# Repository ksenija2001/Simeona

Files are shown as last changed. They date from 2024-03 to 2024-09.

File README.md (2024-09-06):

## Components

| Name | Datasheet | Function  | Quantity |
|:-:|:-:|:-:|:-:|
|  DCGM-3865-12V-EN-240RPM | [datasheet](https://www.waveshare.com/wiki/DCGM-3865-12V-EN-240RPM) | Motor | 2 |
|  NUCLEO-F411RE |  [datasheet](https://www.st.com/content/ccc/resource/technical/document/data_brief/c8/3c/30/f7/d6/08/4a/26/DM00105918.pdf/files/DM00105918.pdf/jcr:content/translations/en.DM00105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)|  Microcontroller | 1 | 
|  Raspberry Pi 4B, 4GB |  [datasheet](https://datasheets.raspberrypi.com/rpi4/raspberry-pi-4-datasheet.pdf) |  Mini-PC |  1 |
|  ROB-14451 |  [datasheet](https://eu.mouser.com/datasheet/2/830/TB6612FNG_datasheet_en_20141001-2528981.pdf) |  Driver | 1 |
|  Slamtec RPLIDAR A2 |  [datasheet](https://bucket-download.slamtec.com/f65f8e37026796c56ddd512d33c7d4308d9edf94/LD310_SLAMTEC_rplidar_datasheet_A2M12_v1.0_en.pdf) |  LIDAR | 1 |
|  TOF |  [datasheet](https://www.waveshare.com/wiki/TOF_Laser_Range_Sensor) |  TOF | 1 |
|  Raspberry Pi Camera Module 3 | |  Camera | 1 |
|  DC/DC XL4015 |  Output 1.25-36V, 5A  |  Step down | 1 |
|  3s Battery  | 2200mah, 11.1V |  Battery | 1 |
|  USB A - USB mini B |  |  Cable | 1 |

## Additional material

<center>
  
| Function | Specification | Quantity  |  Placement |
|:-:|:-:|:-:| :-:|
|  O-ring | 64x3mm | 6 | On wheels |
|  Nucleo mounting screws |  M3x8mm |  3 | Middle level | 
|  RPi4 mounting screws |  M2x20mm |  4 |  Middle level |
|  Step down mounting screws |  M3x10mm |  2 | Bottom level |
|  LIDAR mounting screws |  M3x10mm |  4 | Top level |
|  Motor mounting screws |  M3x16mm |  8 | Bottom level |
|  TOF mounting screws |  M2x10mm |  2 | Bottom level |
|  Battery cover screws |  M3x12mm |  2 | Battery cover |
|  Connecting screws |  M3x16mm |  12 | Between levels |
|  Connecting nuts |  M3 |  12 | Between levels |
|  Insert nut |  M3 |  7 | For RPi4 and Nucleo |

</center>

## CAD

All parts which make up the construction are in the folder [parts](parts).

The following table contains all information about 3D printing the provided parts.
A 0.4mm nozzle was used, everything was printed from PLA on a Bambu A1 Mini.

| Name | Infill | Walls  |  Layer height | Plastic |
|:-:|:-:|:-:| :-:| :-:|
|  Bottom | 20 | 2 | 0.2 | 123g |
|  Middle | 20 | 2 | 0.2 |  63g |
|  Top | 20 | 2 | 0.2 |  60g |
|  Wheel  | 40 | 2 | 0.2 |  20g |
|  Battery cover | 15 | 2 | 0.2 | 17g |

TIP: Hot glue the nut holes when you insert them so they don't fall out every time you have to disassemble it.

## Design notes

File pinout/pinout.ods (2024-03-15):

 | Name | Type | Signal | Label | AF0 | AF1 | AF2 | AF3 | AF4 | AF5 | AF6 | AF7 | AF8 | AF9 | AF10 | AF11 | AF12
1 | VBAT | Power
2 | PC13-ANTI_TAMP | I/O | GPIO_EXTI13 | B1 [Blue PushButton]
3 | PC14-OSC32_IN | I/O | RCC_OSC32_IN
4 | PC15-OSC32_OUT | I/O | RCC_OSC32_OUT
5 | PH0 - OSC_IN | I/O | RCC_OSC_IN
6 | PH1 - OSC_OUT | I/O | RCC_OSC_OUT
7 | NRST | Reset
8 | PC0 | I/O
9 | PC1 | I/O
10 | PC2 | I/O |  |  |  |  |  |  |  | SPI2_MISO | I2S2_ext_SD
11 | PC3 | I/O |  |  |  |  |  |  |  | I2S2_SD/SPI2_MOSI
12 | VSSA | Power
13 | VDDA | Power
14 | PA0-WKUP | I/O |  |  |  | TIM2_CH1/TIM2_ETR | TIM5_CH1 |  |  |  |  | USART2_CTS
15 | PA1 | I/O |  |  |  | TIM2_CH2 | TIM5_CH2 |  |  | I2S4_SD/SPI4_MOSI |  | USART2_RTS
16 | PA2 | I/O |  |  |  | TIM2_CH3 | TIM5_CH3 | TIM9_CH1 |  | I2S_CKIN |  | USART2_TX
17 | PA3 | I/O |  |  |  | TIM2_CH4 | TIM5_CH4 | TIM9_CH2 |  | I2S2_MCK |  | USART2_RX
18 | VSS | Power
19 | VDD | Power
20 | PA4 | I/O |  |  |  |  |  |  |  | I2S1_WS/SPI1_NSS | I2S3_WS/SPI3_NSS | USART2_CK
21 | PA5 | Output | GPIO_Output | LD2 [Green Led] |  | TIM2_CH1/TIM2_ETR |  |  |  | I2S1_CK/SPI1_SCK
22 | PA6 | I/O |  |  |  | TIM1_BKIN | TIM3_CH1 |  |  | SPI1_MISO | I2S2_MCK |  |  |  |  |  | SDIO_CMD
23 | PA7 | I/O |  |  |  | TIM1_CH1N | TIM3_CH2 |  |  | I2S1_SD/SPI1_MOSI
24 | PC4 | I/O
25 | PC5 | I/O
26 | PB0 | I/O |  |  |  | TIM1_CH2N | TIM3_CH3 |  |  |  | I2S5_CK/SPI5_SCK
27 | PB1 | I/O |  |  |  | TIM1_CH3N | TIM3_CH4 |  |  |  | I2S5_WS/SPI5_NSS
28 | PB2 | I/O
29 | PB10 | I/O |  |  |  | TIM2_CH3 |  |  | I2C2_SCL | I2S2_CK/SPI2_SCK | I2S3_MCK |  |  |  |  |  | SDIO_D7
30 | VCAP1 | Power
31 | VSS | Power
32 | VDD | Power
33 | PB12 | I/O |  |  |  | TIM1_BKIN |  |  | I2C2_SMBA | I2S2_WS/SPI2_NSS | I2S4_WS/SPI4_NSS | I2S3_CK/SPI3_SCK
34 | PB13 | I/O |  |  |  | TIM1_CH1N |  |  |  | I2S2_CK/SPI2_SCK | I2S4_CK/SPI4_SCK
35 | PB14 | I/O |  |  |  | TIM1_CH2N |  |  |  | SPI2_MISO | I2S2_ext_SD |  |  |  |  |  | SDIO_D6
36 | PB15 | I/O |  |  | RTC_REFIN | TIM1_CH3N |  |  |  | I2S2_SD/SPI2_MOSI |  |  |  |  |  |  | SDIO_CK
37 | PC6 | I/O |  |  |  |  | TIM3_CH1 |  |  | I2S2_MCK |  |  | USART6_TX |  |  |  | SDIO_D6
38 | PC7 | I/O |  |  |  |  | TIM3_CH2 |  |  | I2S2_CK/SPI2_SCK | I2S3_MCK |  | USART6_RX |  |  |  | SDIO_D7
39 | PC8 | I/O |  |  |  |  | TIM3_CH3 |  |  |  |  |  | USART6_CK |  |  |  | SDIO_D0
40 | PC9 | I/O |  |  | RCC_MCO_2 |  | TIM3_CH4 |  | I2C3_SDA | I2S_CKIN |  |  |  |  |  |  | SDIO_D1
41 | PA8 | I/O |  |  | RCC_MCO_1 | TIM1_CH1 |  |  | I2C3_SCL |  |  | USART1_CK |  |  | USB_OTG_FS_SOF |  | SDIO_D1
42 | PA9 | I/O |  |  |  | TIM1_CH2 |  |  | I2C3_SMBA |  |  | USART1_TX |  |  | USB_OTG_FS_VBUS |  | SDIO_D2
43 | PA10 | I/O |  |  |  | TIM1_CH3 |  |  |  |  | I2S5_SD/SPI5_MOSI | USART1_RX |  |  | USB_OTG_FS_ID
44 | PA11 | I/O |  |  |  | TIM1_CH4 |  |  |  |  | SPI4_MISO | USART1_CTS | USART6_TX |  | USB_OTG_FS_DM
45 | PA12 | I/O |  |  |  | TIM1_ETR |  |  |  |  | SPI5_MISO | USART1_RTS | USART6_RX |  | USB_OTG_FS_DP
46 | PA13 | I/O | SYS_JTMS-SWDIO | TMS | SYS_JTMS-SWDIO
47 | VSS | Power
48 | VDD | Power
49 | PA14 | I/O | SYS_JTCK-SWCLK | TCK | SYS_JTCK-SWCLK
50 | PA15 | I/O |  |  | SYS_JTDI | TIM2_CH1/TIM2_ETR |  |  |  | I2S1_WS/SPI1_NSS | I2S3_WS/SPI3_NSS | USART1_TX
51 | PC10 | I/O |  |  |  |  |  |  |  |  | I2S3_CK/SPI3_SCK |  |  |  |  |  | SDIO_D2
52 | PC11 | I/O |  |  |  |  |  |  |  | I2S3_ext_SD | SPI3_MISO |  |  |  |  |  | SDIO_D3
53 | PC12 | I/O |  |  |  |  |  |  |  |  | I2S3_SD/SPI3_MOSI |  |  |  |  |  | SDIO_CK
54 | PD2 | I/O |  |  |  |  | TIM3_ETR |  |  |  |  |  |  |  |  |  | SDIO_CMD
55 | PB3 | I/O | SYS_JTDO-SWO | SWO | SYS_JTDO-SWO | TIM2_CH2 |  |  |  | I2S1_CK/SPI1_SCK | I2S3_CK/SPI3_SCK | USART1_RX |  | I2C2_SDA
56 | PB4 | I/O |  |  | SYS_JTRST |  | TIM3_CH1 |  |  | SPI1_MISO | SPI3_MISO | I2S3_ext_SD |  | I2C3_SDA |  |  | SDIO_D0
57 | PB5 | I/O |  |  |  |  | TIM3_CH2 |  | I2C1_SMBA | I2S1_SD/SPI1_MOSI | I2S3_SD/SPI3_MOSI |  |  |  |  |  | SDIO_D3
58 | PB6 | I/O |  |  |  |  | TIM4_CH1 |  | I2C1_SCL |  |  | USART1_TX
59 | PB7 | I/O |  |  |  |  | TIM4_CH2 |  | I2C1_SDA |  |  | USART1_RX |  |  |  |  | SDIO_D0
60 | BOOT0 | Boot
61 | PB8 | I/O |  |  |  |  | TIM4_CH3 | TIM10_CH1 | I2C1_SCL |  | I2S5_SD/SPI5_MOSI |  |  | I2C3_SDA |  |  | SDIO_D4
62 | PB9 | I/O |  |  |  |  | TIM4_CH4 | TIM11_CH1 | I2C1_SDA | I2S2_WS/SPI2_NSS |  |  |  | I2C2_SDA |  |  | SDIO_D5
63 | VSS | Power
64 | VDD | Power

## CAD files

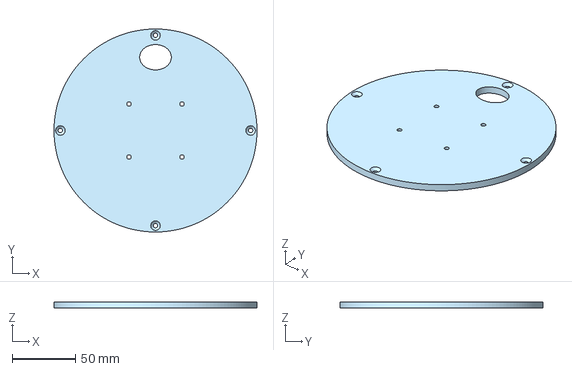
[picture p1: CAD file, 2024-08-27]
parts/Top.3mf
160.0 x 160.0 x 5.00 mm

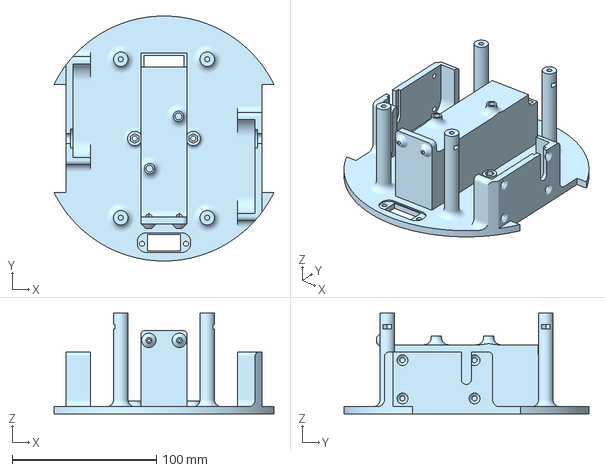
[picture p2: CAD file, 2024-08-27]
parts/Bottom.3mf
152.6 x 170.0 x 70.0 mm

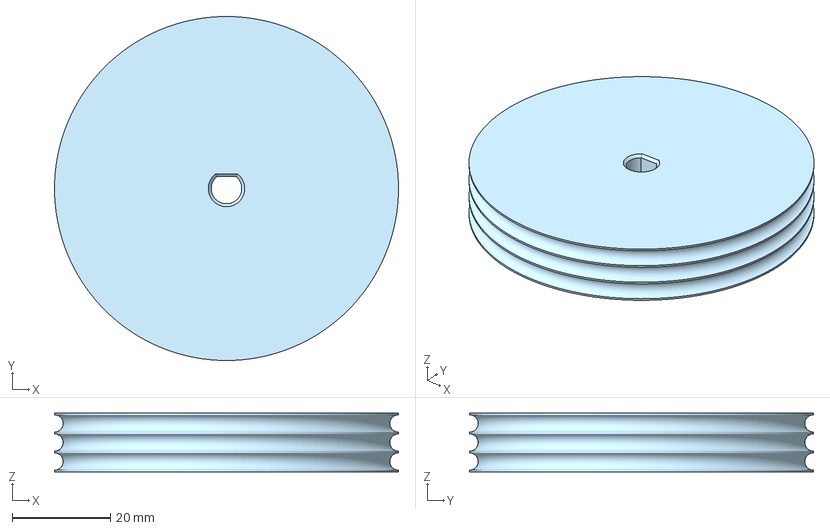
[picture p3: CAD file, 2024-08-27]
parts/Wheel.3mf
70.0 x 70.0 x 12.0 mm

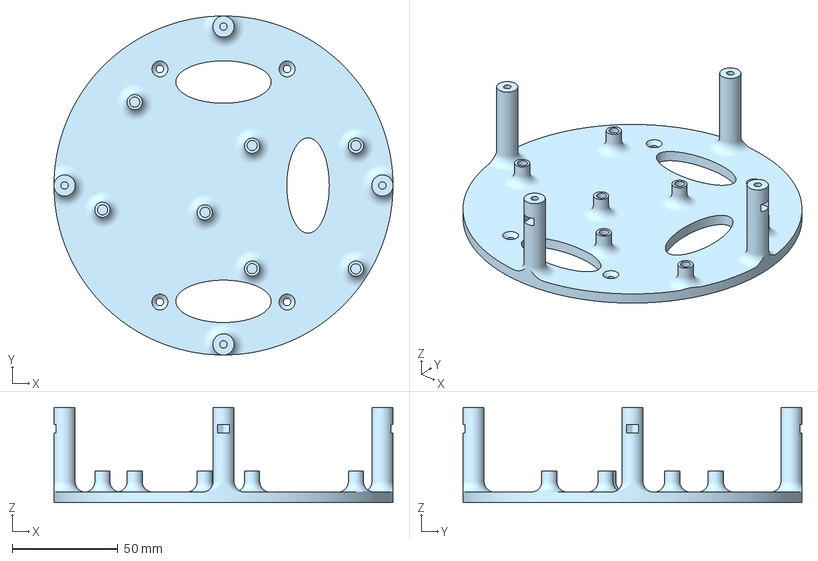
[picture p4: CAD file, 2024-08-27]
parts/Middle.3mf
160.0 x 160.0 x 45.0 mm

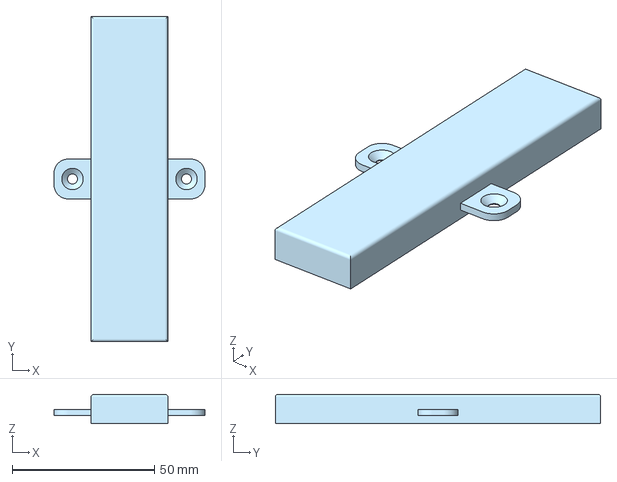
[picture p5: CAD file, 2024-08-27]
parts/Battery_Cover.3mf
53.0 x 114.2 x 10.3 mm

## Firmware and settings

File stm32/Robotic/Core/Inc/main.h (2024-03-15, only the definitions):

#define B1_Pin GPIO_PIN_13
#define B1_GPIO_Port GPIOC
#define TMS_Pin GPIO_PIN_13
#define TMS_GPIO_Port GPIOA
#define TCK_Pin GPIO_PIN_14
#define TCK_GPIO_Port GPIOA
#define SWO_Pin GPIO_PIN_3
#define SWO_GPIO_Port GPIOB

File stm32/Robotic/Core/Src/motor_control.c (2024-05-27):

/*
 * motor_control.c
 *
 *  Created on: Mar 14, 2024
 *      Author: xenia
 */

#include "motor_control.h"

float q0;
float q1;
float q2;

volatile uint32_t interrupt_counter = 0;
float send_odom[7];


sOutput_t BI2  = { .port = GPIOB, .pin = 10 };
sOutput_t BI1  = { .port = GPIOC, .pin = 7 };
sOutput_t AI2  = { .port = GPIOA, .pin = 5};
sOutput_t AI1  = { .port = GPIOB, .pin = 6};
sOutput_t PWMA = { .port = GPIOA, .pin = 0};
sOutput_t PWMB = { .port = GPIOA, .pin = 1};

sMotor_t left_motor = {
		.target_speed = 0,
		.current_speed = 0,
		.control_PWM = 0,
		.errors = {0, 0, 0},
		.Kp = 8,
		.Ki = 0.08,
		.Kd = 0.12,
};
sMotor_t right_motor= {
		.target_speed = 0,
		.current_speed = 0,
		.control_PWM = 0,
		.errors = {0, 0, 0},
		.Kp = 8,
		.Ki = 0.08,
		.Kd = 0.12,
};



// TIM2 CH1 and CH2 configuration as PWM output
// Driver direction pins configuration
void Motors_Init()
{
	left_motor.Compute_PID = Compute_PID;
	right_motor.Compute_PID = Compute_PID;

	// Enabe GPIOA (PWM port), GPIOB and GPIOC clock source
	RCC->AHB1ENR |= ( RCC_AHB1ENR_GPIOAEN );
	RCC->AHB1ENR |= ( RCC_AHB1ENR_GPIOBEN );
	RCC->AHB1ENR |= ( RCC_AHB1ENR_GPIOCEN );

	// Enable TIM2 (PWM source) clock source - 84Mhz
	RCC->APB1ENR |= ( RCC_APB1ENR_TIM2EN );

	// Set PWM source channel pins PA0 (CH1) and PA1 (CH2)
	// to alternate function mode AF1
	PWMA.port->MODER &= ~(0b11 << 2*PWMA.pin);
	PWMA.port->MODER |=  (0b10 << 2*PWMA.pin);
	PWMB.port->MODER &= ~(0b11 << 2*PWMB.pin);
	PWMB.port->MODER |=  (0b10 << 2*PWMB.pin);

	PWMA.port->AFR[0] &= ~(0b1111 << 4*PWMA.pin);
	PWMA.port->AFR[0] |=  (0b0001 << 4*PWMA.pin);
	PWMB.port->AFR[0] &= ~(0b1111 << 4*PWMB.pin);
	PWMB.port->AFR[0] |=  (0b0001 << 4*PWMB.pin);

	// Autoreload value determines the frequency of
	// the PWM signal - 84MHz -> 20kHz
	TIM2->PSC = 1 - 1;
	TIM2->ARR = PWM_ARR;

	// PWM mode 1 - channel is active as long as
	// TIM2->CNT < TIM2->CCR1 - during the timer period
	TIM2->CCMR1 &= ~(0b111 << TIM_CCMR1_OC1M_Pos | 0b111 << TIM_CCMR1_OC2M_Pos);
	TIM2->CCMR1 |=  (0b110 << TIM_CCMR1_OC1M_Pos | 0b110 << TIM_CCMR1_OC2M_Pos);

	// Enable preload for TIM2
	TIM2->CCMR1 |= (0b1 << TIM_CCMR1_OC1PE_Pos | 0b1 << TIM_CCMR1_OC2PE_Pos);

	// Enable autoreload for TIM2
	TIM2->CR1 |= (0b1 << TIM_CR1_ARPE_Pos);

	// Enable automatic update of registers
	TIM2->EGR |= (0b1 << TIM_EGR_UG_Pos);

	// Enable capture/compare as output
	// (PWM output to driver) for CH1 and CH2
	// Default falling edge mode
	TIM2->CCER |= (0b1 << TIM_CCER_CC1E_Pos | 0b1 << TIM_CCER_CC2E_Pos);

	// Enable PWM generation in default edge aligned mode
	TIM2->CR1 |= (0b1 << TIM_CR1_CEN_Pos);



	// Configure pins for driver direction as
	// general purpose output pins
	BI2.port->MODER &= ~(0b11 << 2*BI2.pin);
	BI2.port->MODER |=  (0b01 << 2*BI2.pin);

	BI1.port->MODER &= ~(0b11 << 2*BI1.pin);
	BI1.port->MODER |=  (0b01 << 2*BI1.pin);

	AI1.port->MODER &= ~(0b11 << 2*AI1.pin);
	AI1.port->MODER |=  (0b01 << 2*AI1.pin);

	AI2.port->MODER &= ~(0b11 << 2*AI2.pin);
	AI2.port->MODER |=  (0b01 << 2*AI2.pin);

	// Configure pins for driver direction as
	// output push pull (reset state)
	BI2.port->OTYPER &=  ~(0b1 << BI2.pin);
	BI1.port->OTYPER &=  ~(0b1 << BI1.pin);
	AI1.port->OTYPER &=  ~(0b1 << AI1.pin);
	AI2.port->OTYPER &=  ~(0b1 << AI2.pin);
}

// Configures timer TIM11 with interrupt every 10ms which executes
// PID computation and updates odometry data
void PID_Odom_Interrupt_Init()
{
	// Lower priority than UART IRQHandler and UART buffer checking
	uint32_t tim10_pri_encoding = NVIC_EncodePriority(0, 1, 2);

	// Clock source for TIM10
	RCC->APB2ENR |= ( RCC_APB2ENR_TIM10EN );

	// Clock setup for TIM10, 10ms
	TIM10->PSC = 13 - 1;
	TIM10->ARR = 60000 - 1;

	// Enable immediate update of register on counter
	TIM10->EGR |= ( TIM_EGR_UG );

	// Enable interrupts for TIM10
	TIM10->DIER |= ( TIM_DIER_UIE );

	// Enable counter for TIM10
	TIM10->CR1 |= ( TIM_CR1_CEN );

	// Setup the NVIC to enable interrupts.
	NVIC_SetPriorityGrouping( 0 );
	NVIC_SetPriority( TIM1_UP_TIM10_IRQn, tim10_pri_encoding );
	NVIC_EnableIRQ( TIM1_UP_TIM10_IRQn );
}

void TIM1_UP_TIM10_IRQHandler(void)
{;
	interrupt_counter += 10;

	// Calculates new position and orientation based on encoder output
	// and sends odometry data via UART
	if( interrupt_counter % ODOM_TIME == 0 ){
		sOdom_t* odom = Read_Encoders();

		send_odom[0] = odom->x;
		send_odom[1] = odom->y;
		send_odom[2] = odom->theta;
		send_odom[3] = odom->left_speed;
		send_odom[4] = odom->right_speed;
		send_odom[5] = odom->left_inc;
		send_odom[6] = odom->right_inc;

		left_motor.current_speed = odom->left_speed;
		right_motor.current_speed = odom->right_speed;

		Send_Command(ODOM_TRANSMIT, send_odom, sizeof(send_odom));
	}

	// Calculates speed loop PID and sends the output to the driver
	if( interrupt_counter % PID_TIME == 0 ){
		left_motor.Compute_PID(&left_motor);
		right_motor.Compute_PID(&right_motor);

		Set_Motor_Direction(left_motor.control_PWM, right_motor.control_PWM);
		Set_Motor_PWM(abs(left_motor.control_PWM), abs(right_motor.control_PWM));
	}

	// Clears interrupt flag so that other interrupts can work
	TIM10->SR &= ~TIM_SR_UIF;
}

// Sets target speed for speed loop
void Set_Motor_Speed(float left, float right)
{
	left_motor.target_speed = left;
	right_motor.target_speed = right;

//	left_motor.control_PWM = 0;
//	memset(left_motor.errors, 0, sizeof left_motor.errors);
//
//	right_motor.control_PWM = 0;
//	memset(right_motor.errors, 0, sizeof right_motor.errors);
}

// Updates PWM control for reaching and holding target speed
void Compute_PID(sMotor_t *self){
	self->errors[2] = self->errors[1];
	self->errors[1] = self->errors[0];
	self->errors[0] = self->target_speed - self->current_speed;

	q0 = self->Kp + self->Kd/PID_TIME;
	q1 = self->Ki*PID_TIME - 2*self->Kd/PID_TIME - self->Kp;
	q2 = - self->Kd/PID_TIME;

	self->control_PWM += q0 * self->errors[0] + q1 * self->errors[1] + q2 * self->errors[2];
}

// Changes motor direction based on sign of received speeds
void Set_Motor_Direction(int left, int right)
{
	if (left > 0){ // counter clockwise
		Set_Pin(AI1, 0);
		Set_Pin(AI2, 1);
	}
	else{ // clockwise
		Set_Pin(AI1, 1);
		Set_Pin(AI2, 0);
	}

	if (right > 0){ // counter clockwise
		Set_Pin(BI1, 0);
		Set_Pin(BI2, 1);
	}
	else{ // clockwise
		Set_Pin(BI1, 1);
		Set_Pin(BI2, 0);
	}
}

// Sets motor PWM value caclulated in speed loop
void Set_Motor_PWM(unsigned int left, unsigned int right)
{
	// CCR1 value determines the duty cycle of the
	// PWM signal, min - 0, max - PWM_ARR
	if (left > PWM_ARR) left = PWM_ARR;
	if (right > PWM_ARR) right = PWM_ARR;

	TIM2->CCR1 = left;
	TIM2->CCR2 = right;
}

// Sets or resets a pin
void Set_Pin(sOutput_t output, int value){
	if (value > 0) output.port->BSRR |= (0b1 << output.pin);
	else output.port->BSRR |= (0b1 << (output.pin + 16));
}

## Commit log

2024-03-15 STM32 motors, encoders, uart
    TIM10 and TIM11 interrupts conflicting with each other and TIM2
    [pinout.ods]
2024-03-15 Timer conflicts fixed
2024-03-17 Working version of nucleo code
    Odom, speed loop and motor control working. Robot can reach and hold given speed.
2024-03-21 UART communication
    Added receiving end for UART, untested
2024-03-21 Refactoring, ros2
    Organized folders by Ros code and STM code, added architecture for ros2 code
    [pinout.ods]
2024-03-22 Added datasheets for nucleo
    [pinout.ods]
2024-03-22 UART receive
    Testing serial communication and command parsing, not working yet
    [pinout.ods]
2024-03-25 Speed PID
    Configured parameters for PID, documented the process in folder S_PID, added macro with preset messages for setting speeds over UART
2024-03-28 Raspberry pi and Nucleo communication
    Rpi can send speeds to nucleo via /transmit topic, modified length of messages for nucleo
2024-04-03 UART messages tested
    All communication between raspberyy and stm working.
    [pinout.ods]
2024-04-08 LIDAR setup, odometry over lidar test
2024-04-10 Lidar scan and odometry synchonized and showing in rviz
2024-04-16 Testing stm and rpi communication and commands
    [pinout.ods]
2024-04-18 Teleoperation working
    [robotic.urdf]
2024-05-24 PCB files for nucleo shield
    [BOM-PAMI.xlsx, Nucleo Shield - PAMI.f3z]
2024-05-27 Hardware interface for ros2_control
    Hardware interface written, nucleo messages adapted for it, but not tested. Odom message now returns increments for left and right wheels. URDF and gazebo launch files added to description.
    [my_controllers.yaml, robotic.urdf.xacro, ros2_control.xacro]
2024-05-28 TOF sensor, UART over pins enabled
    UART0 over pins GPIO pins 14,15 working on serial port connected to /dev/ttyAMA0. TOF sensor sending distances continuously, movement node only reacts when the distance passes the given threshold and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
    [config.txt, robotic.urdf]
2024-05-28 Distance PID
    Working only when moving forward
2024-06-06 SLAM enabled, manual PID needs work
    Hardware interface adapted, not tested. Description file finished. All dependencies added to CMakeLists. Lidar transform to base_link working. EKF implemented for wheel odometry and lidar odometry, t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
    [robot_controller.yaml, robotic.urdf.xacro]
2024-06-07 Movement node PID working, frame transforms working
    SLAM workiing very well because laser->base_link transform is finally correct in robot URDF. Movement node manipulation through commands working very well - goal_theta is the final angle after movement. All dependencies defined in CMakeLists.txt and package.xml of robotic_pkg, no more need for sllidar package to be a subdirectory.
    [robotic.urdf.xacro]
2024-07-01 Organising stm32
    [config.txt, my_controllers.yaml, robot_controller.yaml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]
2024-08-20 Added pinout diagram
    [pinout.ods]
2024-08-22 Added pinout example
    [pinout.ods]
2024-08-27 Uploaded CAD parts
    [BOM-PAMI.xlsx, Battery_Cover.3mf, Bottom.3mf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]

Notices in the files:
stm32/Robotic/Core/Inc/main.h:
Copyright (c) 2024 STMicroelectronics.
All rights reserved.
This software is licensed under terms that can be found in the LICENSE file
